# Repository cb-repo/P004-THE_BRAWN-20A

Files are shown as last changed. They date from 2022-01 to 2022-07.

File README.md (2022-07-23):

# THE BRAWN v1.0

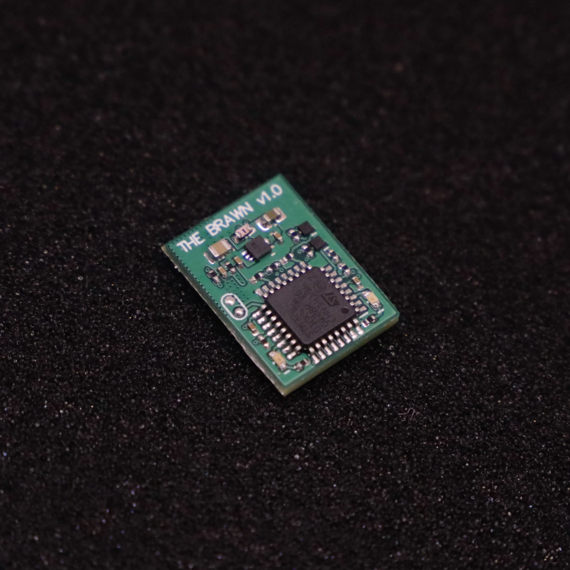
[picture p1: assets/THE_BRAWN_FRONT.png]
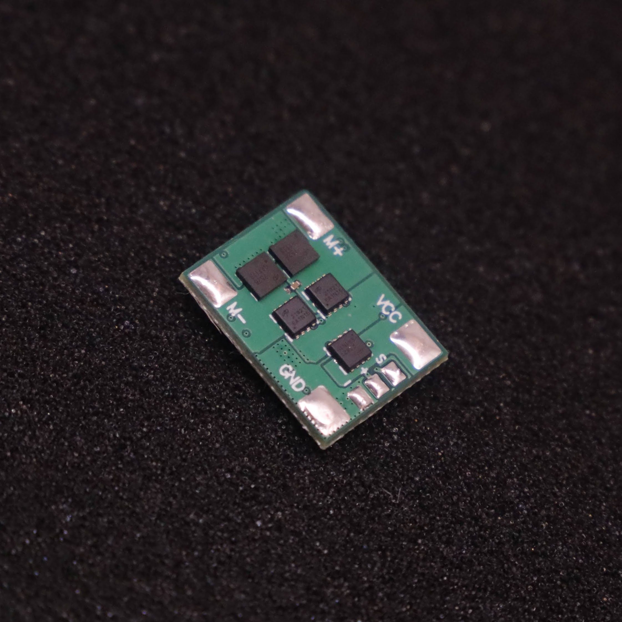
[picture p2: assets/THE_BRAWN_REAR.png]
 

THE BRAWN is a single DC-motor ESC: originally designed for insect-weight combat-robots, but is suitable for any appliction requiring a lightweight motor driver. 

Designed and built in [Christchurch, New Zealand ](https://www.google.co.nz/maps/place/Christchurch+New+Zealand) by Connor Benton, visit [cb-technology](https://www.cb-technology.co.nz/) for details.

## FEATURES
- Single Bi-Directional DC-motor output.
- Ultra-compact and lightweight.
- Under-voltage and reverse-polarity battery input protections.
- Run and status LED's.
- Instant power on and brown out recovery.
- Internal BEC for recievers.
- Includes a 100nF capacitor across the motor output to filter noise and voltage spikes.

## SPECIFICATIONS
- **Dimensions:** 20x15x4 mm
- **Weight:** 1.7g *excluding wires*
- **Input Voltage - Rated:** 1-3S lipo (3.3-12.6V)
- **Input Voltage - Absolute Max:** 18V
- **Output Current - Continuious:** 10A *(for more infomation see the Current Rating seciton)*
- **Output Current - Pulse:** 66A 
- **Motor Braking:** Enabled
- **BEC:** 3.3V, 200mA. Designed to power the radio reciever and other downstream ESC's but no motors or servos.
- **Signal Input:** Standard Servo PWM
     
## Fault Conditions
 - **Under-Voltage:** An under-voltage event occurs when the battery voltage falls below a pre-determined threshold.
    - At 3.6V (per cell) the device enters a warning state. This is only a warning and so functionality is not affected but the warning LED is illuminated for the operator.
    - At 3.4V (per cell) the device enters an under-voltage fault state. All motor functionality will be stopped until battery voltage is restored.
 - **Signal-Input:** A signal-input fault will occur if connection to the radio is lost for 50 ms. 
    - During a signal-input fault, a 'No Signal' fail-safe method is implemented and THE BRAWN will stop driving the motor output.
    - When a radio connection has been re-established the motor functionality is immediately resumed.

## LED Behaviour
There are two LEDs on THE BRAWN: 1x red Run LED and 1x green Status LED. The behaviour of each LED indicates what state the device is in.
 - **Normal Operation** Red: ON, Green: OFF
 - **Warning: Low Battery** Red: ON, Green: Flash
 - **Fault: Under-Voltage:** Red: Flash, Green: Flash
 - **Fault: Signal Input:** Red: OFF, Green: Flash

## Current Rating
The current rating of THE BRAWN is temperature-limited and so is very dependednt on the wires (gauge, length, and insulation) and avalible cooling. It is the responsibility of the user to choose the correct wires and test it appropriately before stressing the THE BRAWN in combat. 

As a guide, constant-current thermal testing has been conducted to illistrate the thermal characteristics. *Note: This test has been conducted at constant current, resulting in a higher temperature than the pulse currents in many drive applications.*

##### Reference testing parameters:
 - **Voltage:** 12V
 - **Motor Wire Length:** 100 mm
 - **Battery Wire Length:** 100 mm
 - **Wire Insulation:** PVC
 - **Ambient Temperature:** 23.5 °C
 - **PCB Heatshrink:** Yes
 - **ESC Cooling:** Open-Air passive cooling

##### Constant Current = 5A

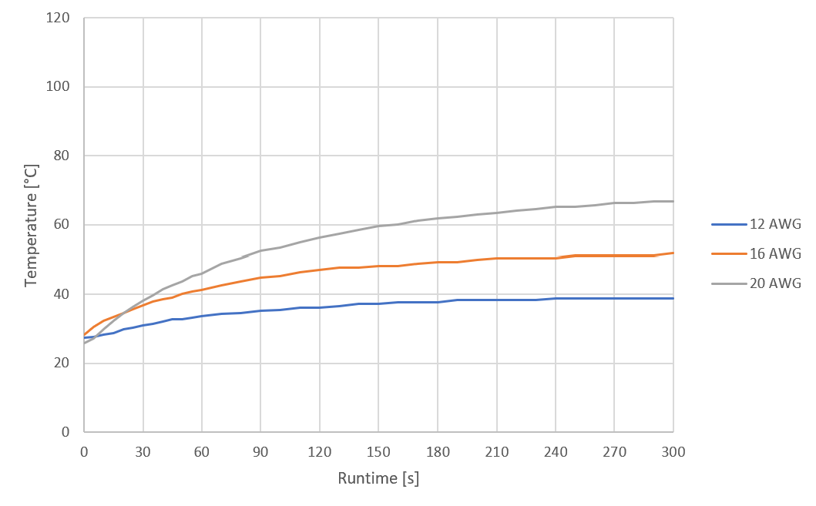
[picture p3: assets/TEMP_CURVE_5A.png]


##### Constant Current = 8A

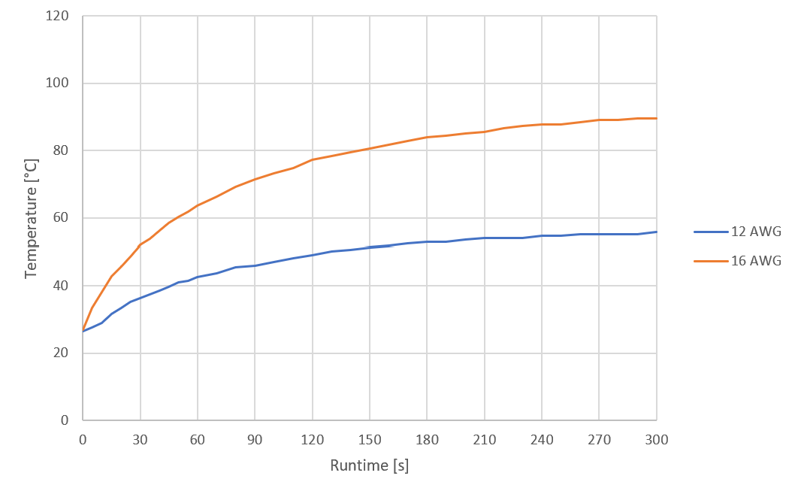
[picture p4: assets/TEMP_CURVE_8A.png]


##### Constant Current = 10A

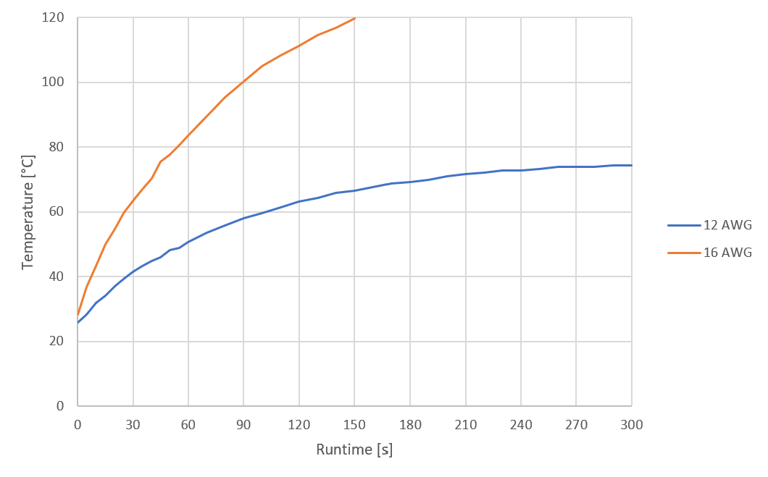
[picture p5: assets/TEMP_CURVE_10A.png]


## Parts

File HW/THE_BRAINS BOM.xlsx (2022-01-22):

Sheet: BOM Report
 |  |  | InFact Ltd.
 |  |  | 5 Amuri Park
 |  |  | 404 Barbadoes Street
 |  |  | Christchurch 8013
 |  |  | New Zealand
 |  | www.infact.co.nz
Bill of Materials |  |  | PXXX-50X - Description
Line | Manufacturer | Manufacturer Part Number | Description | Supplier 1 | Supplier Part Number 1 | Unit Price | Qty | Cost | Ordered | Received | Designator
1 | STMicroelectronics | STM32L051C6T6 | IC MCU 32BIT 32KB FLASH 48LQFP | Digi-Key | 497-15202-ND | $4.82 | 1 | $4.82 | Y | Y | U4
2 | STMicroelectronics | LDL212PUR | IC REG LINEAR POS ADJ 1.2A 6DFN | Digi-Key | 497-16566-1-ND | $0.58 | 1 | $0.58 | Y | Y | U2
3 | Texas Instruments | DRV8837CDSGR | IC HALF-BRIDGE DRVR PWM 8WSON | Digi-Key | 296-47205-1-ND | $1.21 | 2 | $2.42 | Y | Y | U6, U7
4 | Rohm Semiconductor | RQ3E120ATTB | MOSFET P-CH 30V 12A 8HSMT | Digi-Key | RQ3E120ATTBCT-ND | $0.90 | 1 | $0.90 | Y | Y
5 | Murata Electronics North America | BLM15HG102SN1D | FILTER CHIP 1000 OHM 250MA 0402 | Digi-Key | 490-3999-1-ND | $0.06 | 1 | $0.06 |  |  | L1
6 | Stackpole Electronics Inc | CSR0402FKR100 | RES 0.1 OHM 1% 1/8W 0402 | Digi-Key | CSR0402FKR100CT-ND | $0.18 | 1 | $0.18 | Y |  | R2
7 | Samsung Electro-Mechanics | CL21A106KAYNNNG | CAP CER 10UF 25V X5R 0805 | Digi-Key | 1276-6454-1-ND | $0.11 | 1 | $0.11 | Y |  | C7
8 | Bourns Inc. | MF-FSMF020X-2 | PTC RESET FUSE 9V 200MA 0603 | Digi-Key | MF-FSMF020X-2CT-ND | $0.50 | 1 | $0.50 | Y |  | R4
9 | Taiyo Yuden | UMK105CBJ105MV-F | CAP CER 1UF 50V X5R 0402 | Digi-Key | 587-6278-1-ND | $0.16 | 2 | $0.33 | Y | Y | C8, C4
10 | KYOCERA AVX | 0402YD475MAT2A | CAP CER 4.7UF 16V X5R 0402 | Digi-Key | 478-10788-1-ND | $0.18 | 1 | $0.18 | Y | Y | C12
11 | Taiyo Yuden | UMK105B7104KV-FR | CAP CER 0.1UF 50V X7R 0402 | Digi-Key | 587-3498-1-ND | $0.05 | 12 | $0.60 | Y | Y | C1, C2, C6, C9, C10, C11, C13, C15, C18, C19, C20, C21
12 | Lumex Opto/Components Inc | SML-LX0603GW-TR | LED 565NM GRN DIFF 0603 SMD | Digi-Key | 67-1549-1-ND | $0.23 | 1 | $0.23 | Y | Y | DS2
13 | Lumex Opto/Components Inc | SML-LX0603IW-TR | LED 635NM RED DIFF 0603 SMD | Digi-Key | 67-1548-1-ND | $0.23 | 1 | $0.23 | Y | Y | DS1
14 | Vishay Dale | CRCW04021K80FKED | RES 1k8 0.0625W 1% 0402 SMD | Digi-Key | 541-1.80KLCT-ND | $0.01 | 1 | $0.01 | Y | Y | R8
15 | Yageo | RC0402FR-0710KL | RES 10K OHM 1/16W 1% 0402 SMD | Digi-Key | 311-10.0KLRCT-ND | $0.00385 | 7 | $0.03 | Y | Y | R7, R9, R10, R11, R12, R13, R14
16 | Yageo | RC0402FR-07120RL | RES 120 OHM 1/16W 0402 SMD | Digi-Key | 311-120LRCT-ND | $0.00385 | 2 | $0.01 | Y | Y | R5, R15
17 | Yageo | RC0402FR-07150KL | RES SMD 150K OHM 1% 1/16W 0402 | Digi-Key | 311-150KLRCT-ND | $0.01 | 1 | $0.01 | Y | Y | R3
18 | Yageo | RC0402FR-07270KL | RES SMD 270K OHM 1% 1/16W 0402 | Digi-Key | 311-270KLRCT-ND | $0.01 | 1 | $0.01 | Y | Y | R1
19 | JLC PCB |  | PCB |  |  | $5.68 | 1 | $5.68 | Y
20 | Chip Quik Inc. | SMD291AX50T3 | SLDR PASTE NO-CLN SN63/PB37 50G | Digi-Key | SMD291AX50T3-ND | $0.21 | 1 | $0.21 | Y | Y
 |  |  |  |  |  |  | 31 | $17.08
Approved |  |  | Notes
 | Total Order Cost
 | Total Order QTY | 60
 | Unit Cost | $17.08
 | Unit Sell Price | 30
 | Unit Profit | 12.91864
 | Total Profit | 775.1184

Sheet: Sheet1
MCU + FETs | 430.39 | 50 | 8.6078
LDO |  |  | 0.684
Poly-fuse | - | - | 0.4951
22UF Cap | - | - | 0.2248
LED x2 |  |  | 0.4634
Passives |  |  | 0.1282
Solder Paste | - | - | 0.1
PCB | 284.16 | 50 | 5.6832
Assy Labour | 250 | 50 | 5
 |  |  | 21.3865 | Unit Cost
 |  |  | 30 | Unit Sale Price
 |  |  | 8.6135 | Unit Profit
 |  |  | 430.675 | Total Profit

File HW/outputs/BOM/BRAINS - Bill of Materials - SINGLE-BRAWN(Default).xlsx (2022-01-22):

 |  |  | InFact Ltd. | +64 3 3777316
 |  |  | 5 Amuri Park | <Parameter Project_Fax not found>
 |  |  | 404 Barbadoes Street
 |  |  | Christchurch 8013
 |  |  | New Zealand
 |  | www.infact.co.nz
Bill of Materials |  |  | PXXX-50X - Description
Source Data From: |  |  | C:\dev\GitHub\THE_BRAWN\HW\BRAWN.PrjPCB
Project: |  |  | BRAWN.PrjPCB
Revision: |  |  | 0A
Variant: |  |  | Default
Creation Date: |  | 9/12/2021 | 2:01 AM
Print Date: |  | 2021-12-09 | 2:01:45
Line | Manufacturer | Manufacturer Part Number | Description | Fitted | Supplier 1 | Supplier Part Number 1 | Supplier Unit Price 1 | Quantity | Cost | Designator
1 | Taiyo Yuden | UMK105B7104KV-FR | CAP CER 100nF 50V X7R 0402 | Fitted | Digi-Key | 587-3498-1-ND | $0.04 | 1 | $0.04 | C2
2 | Taiyo Yuden | UMK105B7104KV-FR | CAP CER 100nF 50V X7R 0402 | Fitted | Digi-Key | 587-3498-1-ND | $0.04 | 1 | $0.04 | C4
3 | Taiyo Yuden | UMK105B7104KV-FR | CAP CER 100nF 50V X7R 0402 | Fitted | Digi-Key | 587-3498-1-ND | $0.04 | 1 | $0.04 | C8
4 | Taiyo Yuden | UMK105B7104KV-FR | CAP CER 100nF 50V X7R 0402 | Fitted | Digi-Key | 587-3498-1-ND | $0.04 | 1 | $0.04 | C9
5 | Taiyo Yuden | UMK105B7104KV-FR | CAP CER 100nF 50V X7R 0402 | Fitted | Digi-Key | 587-3498-1-ND | $0.04 | 1 | $0.04 | C10
6 | Taiyo Yuden | UMK105B7104KV-FR | CAP CER 100nF 50V X7R 0402 | Fitted | Digi-Key | 587-3498-1-ND | $0.04 | 1 | $0.04 | C12
7 | Samsung Electro-Mechanics | CL21A226KOQNNNE | CAP CER 22UF 16V X5R 0805 | Fitted | Digi-Key | 1276-6526-1-ND | $0.14 | 1 | $0.14 | C3
8 | Samsung Electro-Mechanics | CL21A226KOQNNNE | CAP CER 22UF 16V X5R 0805 | Fitted | Digi-Key | 1276-6526-1-ND | $0.14 | 1 | $0.14 | C7
9 | STMicroelectronics | LDL212PV33R | 1.2A 3V3 LDO LINEAR REGULATOR | Fitted | Digi-Key | 497-19548-1-ND | $0.36 | 1 | $0.36 | U1
10 | STMicroelectronics | STM32L010K4T6 | ARM® Cortex®-M0+ series Microcontroller IC 32-Bit 32MHz 16KB (16K x 8) FLASH 32-LQFP (7x7) | Fitted | Digi-Key | 497-STM32L010K4T6-ND | $1.69 | 1 | $1.69 | U3
11 | Lumex Opto/Components Inc | SML-LX0603GW-TR | LED 565NM GRN DIFF 0603 SMD | Fitted | Digi-Key | 67-1549-1-ND | $0.13 | 1 | $0.13 | DS2
12 | Lumex Opto/Components Inc | SML-LX0603IW-TR | LED 635NM RED DIFF 0603 SMD | Fitted | Digi-Key | 67-1548-1-ND | $0.13 | 1 | $0.13 | DS1
13 |  |  |  | Fitted |  |  |  | 1 | $0.00 | J1
14 |  |  |  | Fitted |  |  |  | 1 | $0.00 | J2
15 |  |  |  | Fitted |  |  |  | 1 | $0.00 | J3
16 |  |  |  | Fitted |  |  |  | 1 | $0.00 | J4
17 |  |  |  | Fitted |  |  |  | 1 | $0.00 | J5
18 |  |  |  | Fitted |  |  |  | 1 | $0.00 | J7
19 |  |  |  | Fitted |  |  |  | 1 | $0.00 | J8
20 |  |  |  | Fitted |  |  |  | 1 | $0.00 | J9
21 |  |  |  | Fitted |  |  |  | 1 | $0.00 | J10
22 | Yageo | RC0402JR-070RL | RES 0R OHM 1/16W 5% 0402 SMD | Fitted | Digi-Key | 311-0.0JRCT-ND | $0.00313 | 1 | $0.00313 | R1
23 | Vishay Dale | CRCW04021K80FKED | RES 1k8 0.0625W 1% 0402 SMD | Fitted | Digi-Key | 541-1.80KLCT-ND | $0.01 | 1 | $0.01 | R13
24 | Yageo | RC0402FR-0710KL | RES 10K OHM 1/16W 1% 0402 SMD | Fitted | Digi-Key | 311-10.0KLRCT-ND | $0.00441 | 1 | $0.00441 | R4
25 | Yageo | RC0402FR-0710KL | RES 10K OHM 1/16W 1% 0402 SMD | Fitted | Digi-Key | 311-10.0KLRCT-ND | $0.00441 | 1 | $0.00441 | R6
26 | Yageo | RC0402FR-0710KL | RES 10K OHM 1/16W 1% 0402 SMD | Fitted | Digi-Key | 311-10.0KLRCT-ND | $0.00441 | 1 | $0.00441 | R7
27 | Yageo | RC0402FR-0710KL | RES 10K OHM 1/16W 1% 0402 SMD | Fitted | Digi-Key | 311-10.0KLRCT-ND | $0.00441 | 1 | $0.00441 | R8
28 | Yageo | RC0402FR-0710KL | RES 10K OHM 1/16W 1% 0402 SMD | Fitted | Digi-Key | 311-10.0KLRCT-ND | $0.00441 | 1 | $0.00441 | R9
29 | Yageo | RC0402FR-0710KL | RES 10K OHM 1/16W 1% 0402 SMD | Fitted | Digi-Key | 311-10.0KLRCT-ND | $0.00441 | 1 | $0.00441 | R10
30 | Yageo | RC0402FR-0710KL | RES 10K OHM 1/16W 1% 0402 SMD | Fitted | Digi-Key | 311-10.0KLRCT-ND | $0.00441 | 1 | $0.00441 | R11
31 | Yageo | RC0402FR-0710KL | RES 10K OHM 1/16W 1% 0402 SMD | Fitted | Digi-Key | 311-10.0KLRCT-ND | $0.00441 | 1 | $0.00441 | R12
32 | Yageo | RC0402FR-07120RL | RES 120 OHM 1/16W 0402 SMD | Fitted | Digi-Key | 311-120LRCT-ND | $0.00441 | 1 | $0.00441 | R14
33 | Yageo | RC0402FR-07120RL | RES 120 OHM 1/16W 0402 SMD | Fitted | Digi-Key | 311-120LRCT-ND | $0.00441 | 1 | $0.00441 | R15
34 | Yageo | RC0603JR-070RL | RES 0.0 OHM 1/10W 0603 SMD | Fitted | Digi-Key | 311-0.0GRCT-ND | $0.00462 | 1 | $0.00462 | R2
35 | Alpha & Omega Semiconductor Inc. | AONR21321 | P-Channel 30 V 24A (Tc) 4.1W (Ta), 24W (Tc) Surface Mount 8-DFN-EP (3x3) | Fitted | Digi-Key | 785-1797-1-ND | $0.28 | 1 | $0.28 | Q1
36 | Alpha & Omega Semiconductor Inc. | AONR21321 | P-Channel 30 V 24A (Tc) 4.1W (Ta), 24W (Tc) Surface Mount 8-DFN-EP (3x3) | Fitted | Digi-Key | 785-1797-1-ND | $0.28 | 1 | $0.28 | Q3
37 | Alpha & Omega Semiconductor Inc. | AONR21321 | P-Channel 30 V 24A (Tc) 4.1W (Ta), 24W (Tc) Surface Mount 8-DFN-EP (3x3) | Fitted | Digi-Key | 785-1797-1-ND | $0.28 | 1 | $0.28 | Q4
38 | Alpha & Omega Semiconductor Inc. | AON7528 | MOSFET N-CH 30V 45A/50A 8DFN | Fitted | Digi-Key | 785-1506-1-ND | $0.64 | 1 | $0.64 | Q6
39 | Alpha & Omega Semiconductor Inc. | AON7528 | MOSFET N-CH 30V 45A/50A 8DFN | Fitted | Digi-Key | 785-1506-1-ND | $0.64 | 1 | $0.64 | Q7
40 | Diodes Incorporated | DMN2450UFD-7 | MOSFET N-CH 20V 900MA 3DFN | Fitted | Digi-Key | DMN2450UFD-7DICT-ND | $0.11 | 1 | $0.11 | Q2
41 | Diodes Incorporated | DMN2450UFD-7 | MOSFET N-CH 20V 900MA 3DFN | Fitted | Digi-Key | DMN2450UFD-7DICT-ND | $0.11 | 1 | $0.11 | Q5
 |  |  |  |  |  |  |  | 41 | $5.22
Approved |  |  | Notes

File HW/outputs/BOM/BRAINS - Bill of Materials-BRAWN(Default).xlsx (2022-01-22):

 |  |  | InFact Ltd. | +64 3 3777316
 |  |  | 5 Amuri Park | <Parameter Project_Fax not found>
 |  |  | 404 Barbadoes Street
 |  |  | Christchurch 8013
 |  |  | New Zealand
 |  | www.infact.co.nz
Bill of Materials |  |  | PXXX-50X - Description
Source Data From: |  |  | C:\dev\GitHub\THE_BRAWN\HW\BRAWN.PrjPCB
Project: |  |  | BRAWN.PrjPCB
Revision: |  |  | 0A
Variant: |  |  | Default
Creation Date: |  | 9/12/2021 | 2:01 AM
Print Date: |  | 2021-12-09 | 2:01:49
Line | Manufacturer | Manufacturer Part Number | Description | Fitted | Supplier 1 | Supplier Part Number 1 | Supplier Unit Price 1 | Quantity | Cost | Designator
1 | Taiyo Yuden | UMK105B7104KV-FR | CAP CER 100nF 50V X7R 0402 | Fitted | Digi-Key | 587-3498-1-ND | $0.03 | 6 | $0.19 | C2, C4, C8, C9, C10, C12
2 | Samsung Electro-Mechanics | CL21A226KOQNNNE | CAP CER 22UF 16V X5R 0805 | Fitted | Digi-Key | 1276-6526-1-ND | $0.14 | 2 | $0.28 | C3, C7
3 | STMicroelectronics | LDL212PV33R | 1.2A 3V3 LDO LINEAR REGULATOR | Fitted | Digi-Key | 497-19548-1-ND | $0.36 | 1 | $0.36 | U1
4 | STMicroelectronics | STM32L010K4T6 | ARM® Cortex®-M0+ series Microcontroller IC 32-Bit 32MHz 16KB (16K x 8) FLASH 32-LQFP (7x7) | Fitted | Digi-Key | 497-STM32L010K4T6-ND | $1.69 | 1 | $1.69 | U3
5 | Lumex Opto/Components Inc | SML-LX0603GW-TR | LED 565NM GRN DIFF 0603 SMD | Fitted | Digi-Key | 67-1549-1-ND | $0.13 | 1 | $0.13 | DS2
6 | Lumex Opto/Components Inc | SML-LX0603IW-TR | LED 635NM RED DIFF 0603 SMD | Fitted | Digi-Key | 67-1548-1-ND | $0.13 | 1 | $0.13 | DS1
7 |  |  |  | Fitted |  |  |  | 9 | $0.00 | J1, J2, J3, J4, J5, J7, J8, J9, J10
8 | Yageo | RC0402JR-070RL | RES 0R OHM 1/16W 5% 0402 SMD | Fitted | Digi-Key | 311-0.0JRCT-ND | $0.00313 | 1 | $0.00313 | R1
9 | Vishay Dale | CRCW04021K80FKED | RES 1k8 0.0625W 1% 0402 SMD | Fitted | Digi-Key | 541-1.80KLCT-ND | $0.01 | 1 | $0.01 | R13
10 | Yageo | RC0402FR-0710KL | RES 10K OHM 1/16W 1% 0402 SMD | Fitted | Digi-Key | 311-10.0KLRCT-ND | $0.00316 | 8 | $0.03 | R4, R6, R7, R8, R9, R10, R11, R12
11 | Yageo | RC0402FR-07120RL | RES 120 OHM 1/16W 0402 SMD | Fitted | Digi-Key | 311-120LRCT-ND | $0.00441 | 2 | $0.01 | R14, R15
12 | Yageo | RC0603JR-070RL | RES 0.0 OHM 1/10W 0603 SMD | Fitted | Digi-Key | 311-0.0GRCT-ND | $0.00462 | 1 | $0.00462 | R2
13 | Alpha & Omega Semiconductor Inc. | AONR21321 | P-Channel 30 V 24A (Tc) 4.1W (Ta), 24W (Tc) Surface Mount 8-DFN-EP (3x3) | Fitted | Digi-Key | 785-1797-1-ND | $0.25 | 3 | $0.75 | Q1, Q3, Q4
14 | Alpha & Omega Semiconductor Inc. | AON7528 | MOSFET N-CH 30V 45A/50A 8DFN | Fitted | Digi-Key | 785-1506-1-ND | $0.64 | 2 | $1.29 | Q6, Q7
15 | Diodes Incorporated | DMN2450UFD-7 | MOSFET N-CH 20V 900MA 3DFN | Fitted | Digi-Key | DMN2450UFD-7DICT-ND | $0.11 | 2 | $0.23 | Q2, Q5
 |  |  |  |  |  |  |  | 41 | $5.10
Approved |  |  | Notes

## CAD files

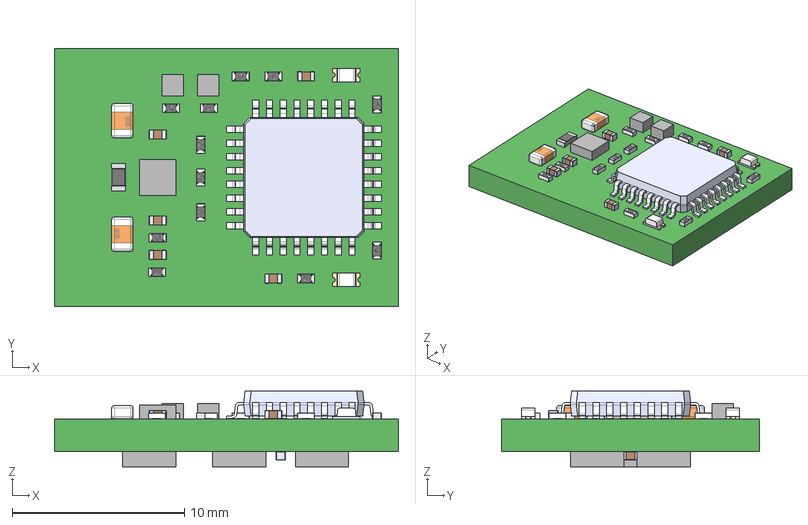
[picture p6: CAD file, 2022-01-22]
HW/outputs/ExportSTEP/BRAWN(Default).step
20.0 x 15.0 x 4.41 mm
TSQFP50P700X700X160-32N
Extruded x 8
User_Library-RESC1005X04N x 12
User_Library-res0603-1
LED_0603 x 2
EVK105RH010BW-F--3DModel-STEP-46669 x 6
User_Library-0805_SMD_Capacitor x 2

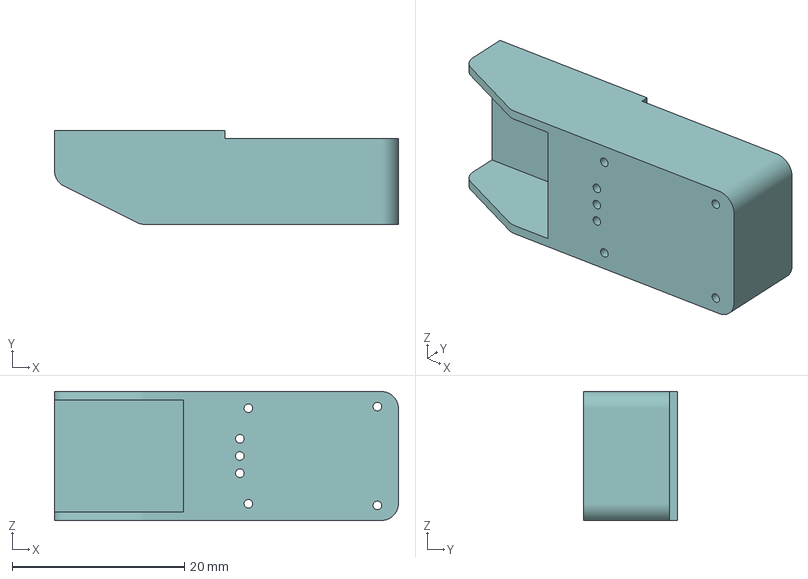
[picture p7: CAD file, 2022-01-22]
MECH/Programmer ClipBottom.3MF
40.0 x 10.9 x 15.0 mm

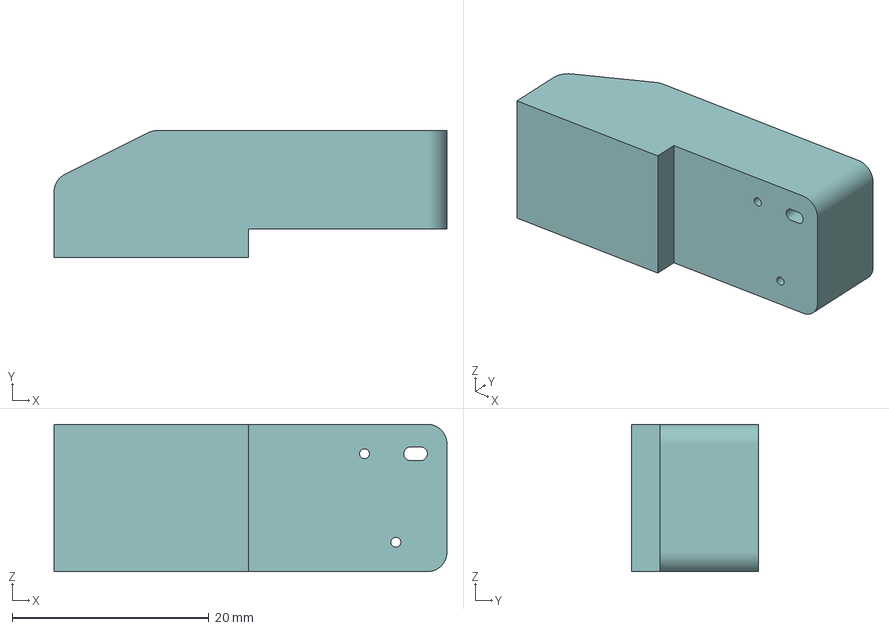
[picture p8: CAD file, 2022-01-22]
MECH/Programmer ClipTop.3MF
40.0 x 12.9 x 15.0 mm

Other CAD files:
MECH/Programmer Clip.SLDPRT

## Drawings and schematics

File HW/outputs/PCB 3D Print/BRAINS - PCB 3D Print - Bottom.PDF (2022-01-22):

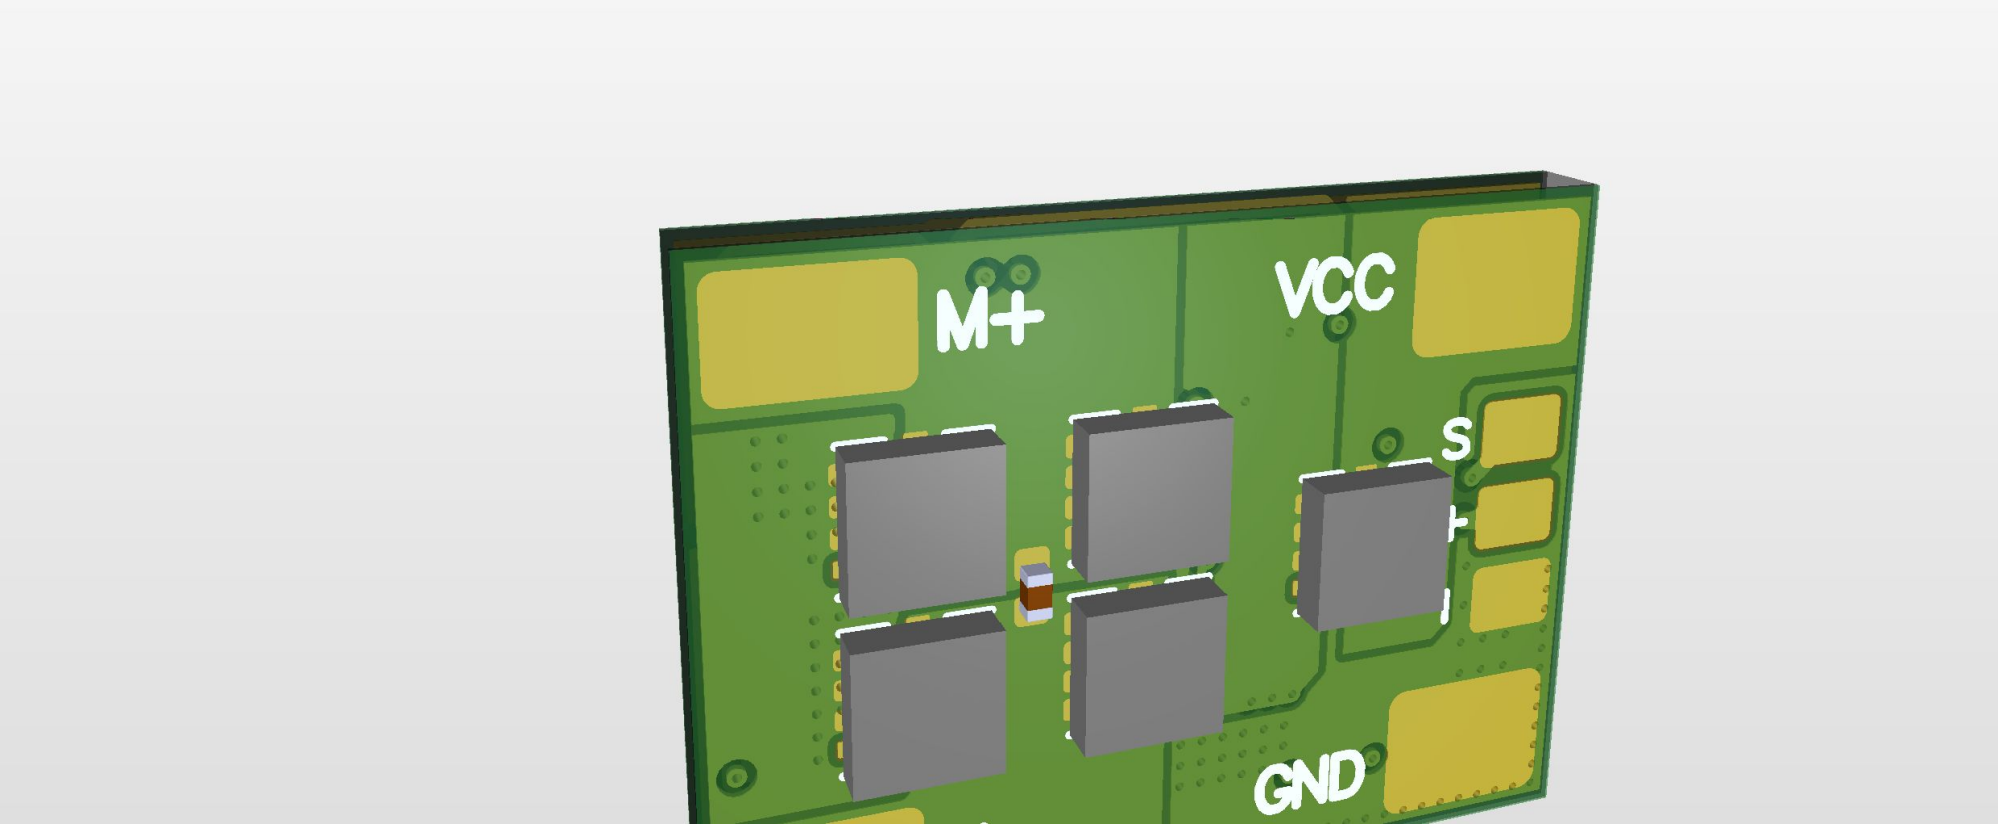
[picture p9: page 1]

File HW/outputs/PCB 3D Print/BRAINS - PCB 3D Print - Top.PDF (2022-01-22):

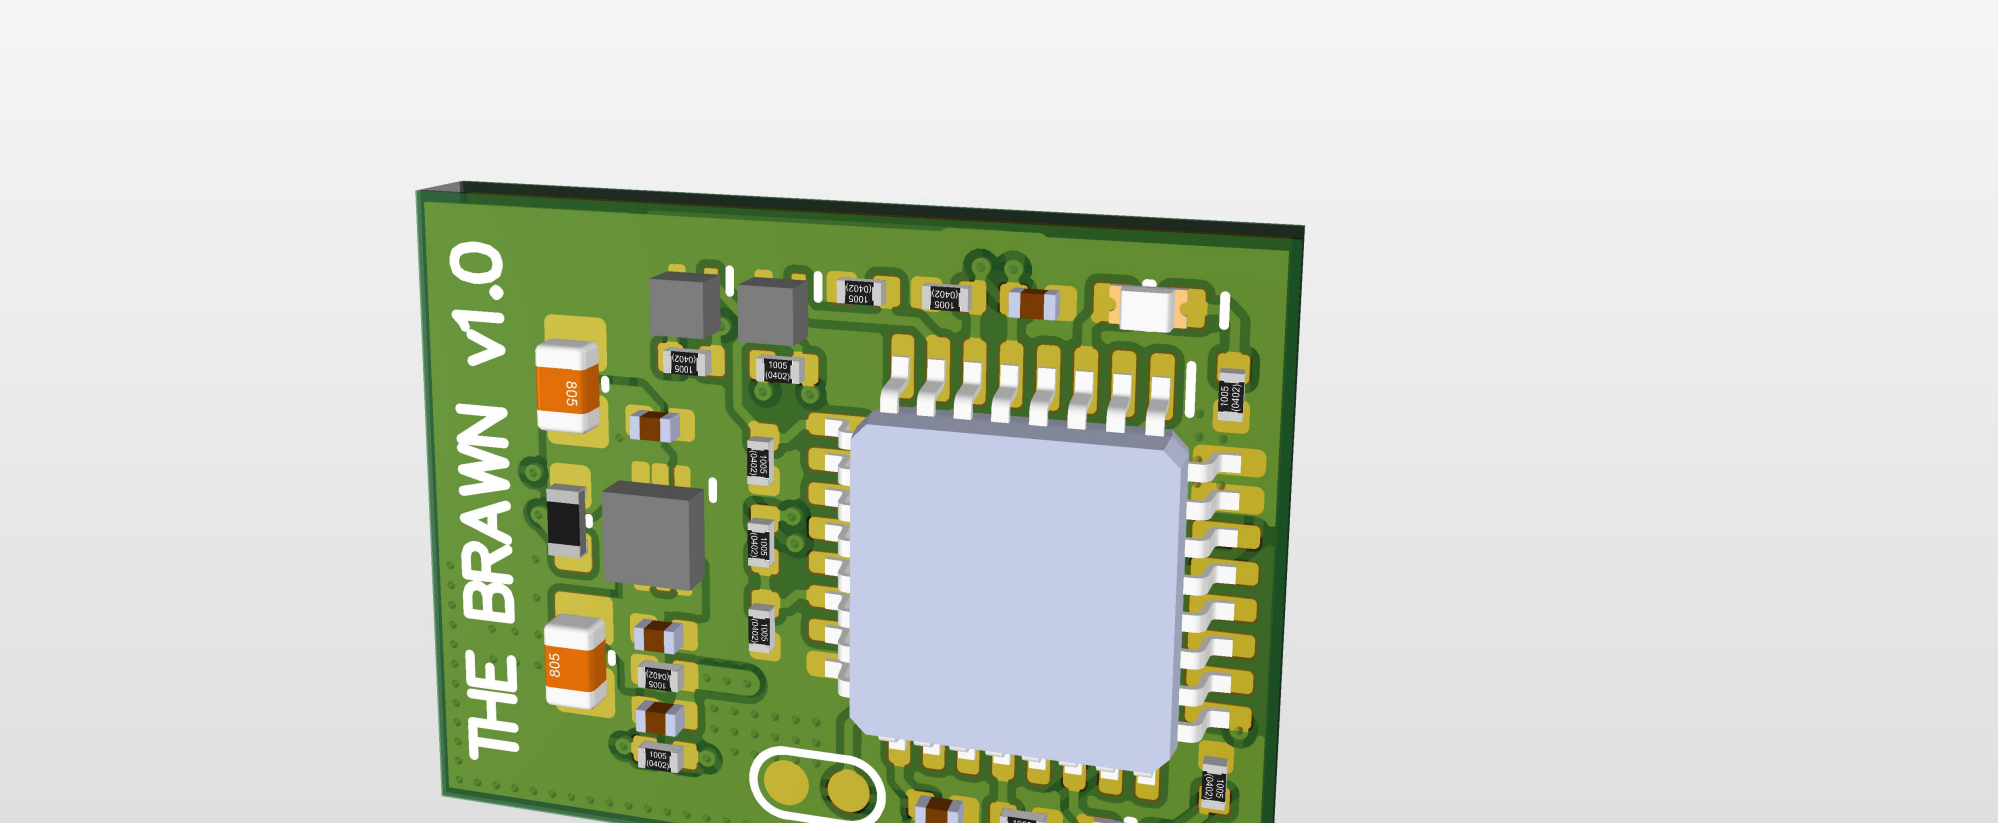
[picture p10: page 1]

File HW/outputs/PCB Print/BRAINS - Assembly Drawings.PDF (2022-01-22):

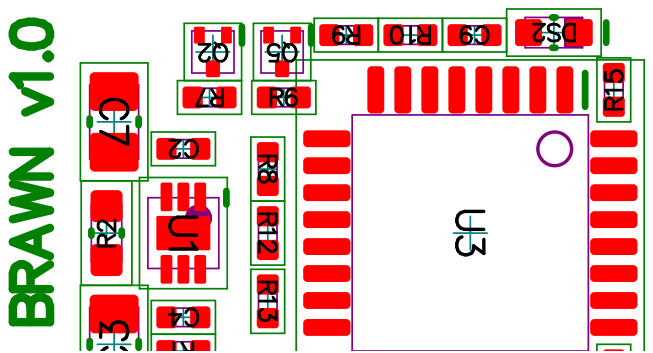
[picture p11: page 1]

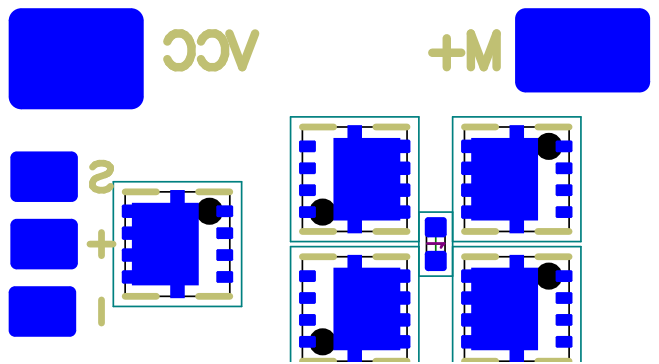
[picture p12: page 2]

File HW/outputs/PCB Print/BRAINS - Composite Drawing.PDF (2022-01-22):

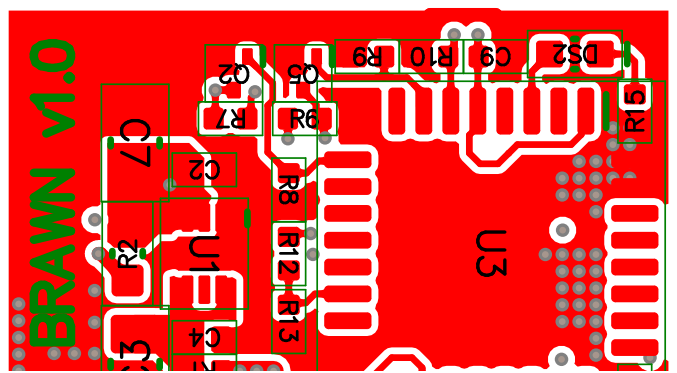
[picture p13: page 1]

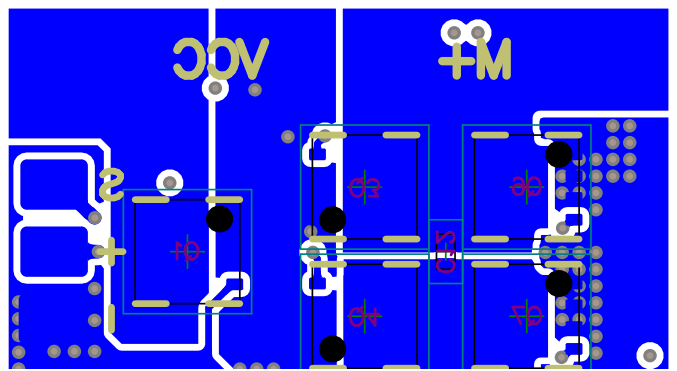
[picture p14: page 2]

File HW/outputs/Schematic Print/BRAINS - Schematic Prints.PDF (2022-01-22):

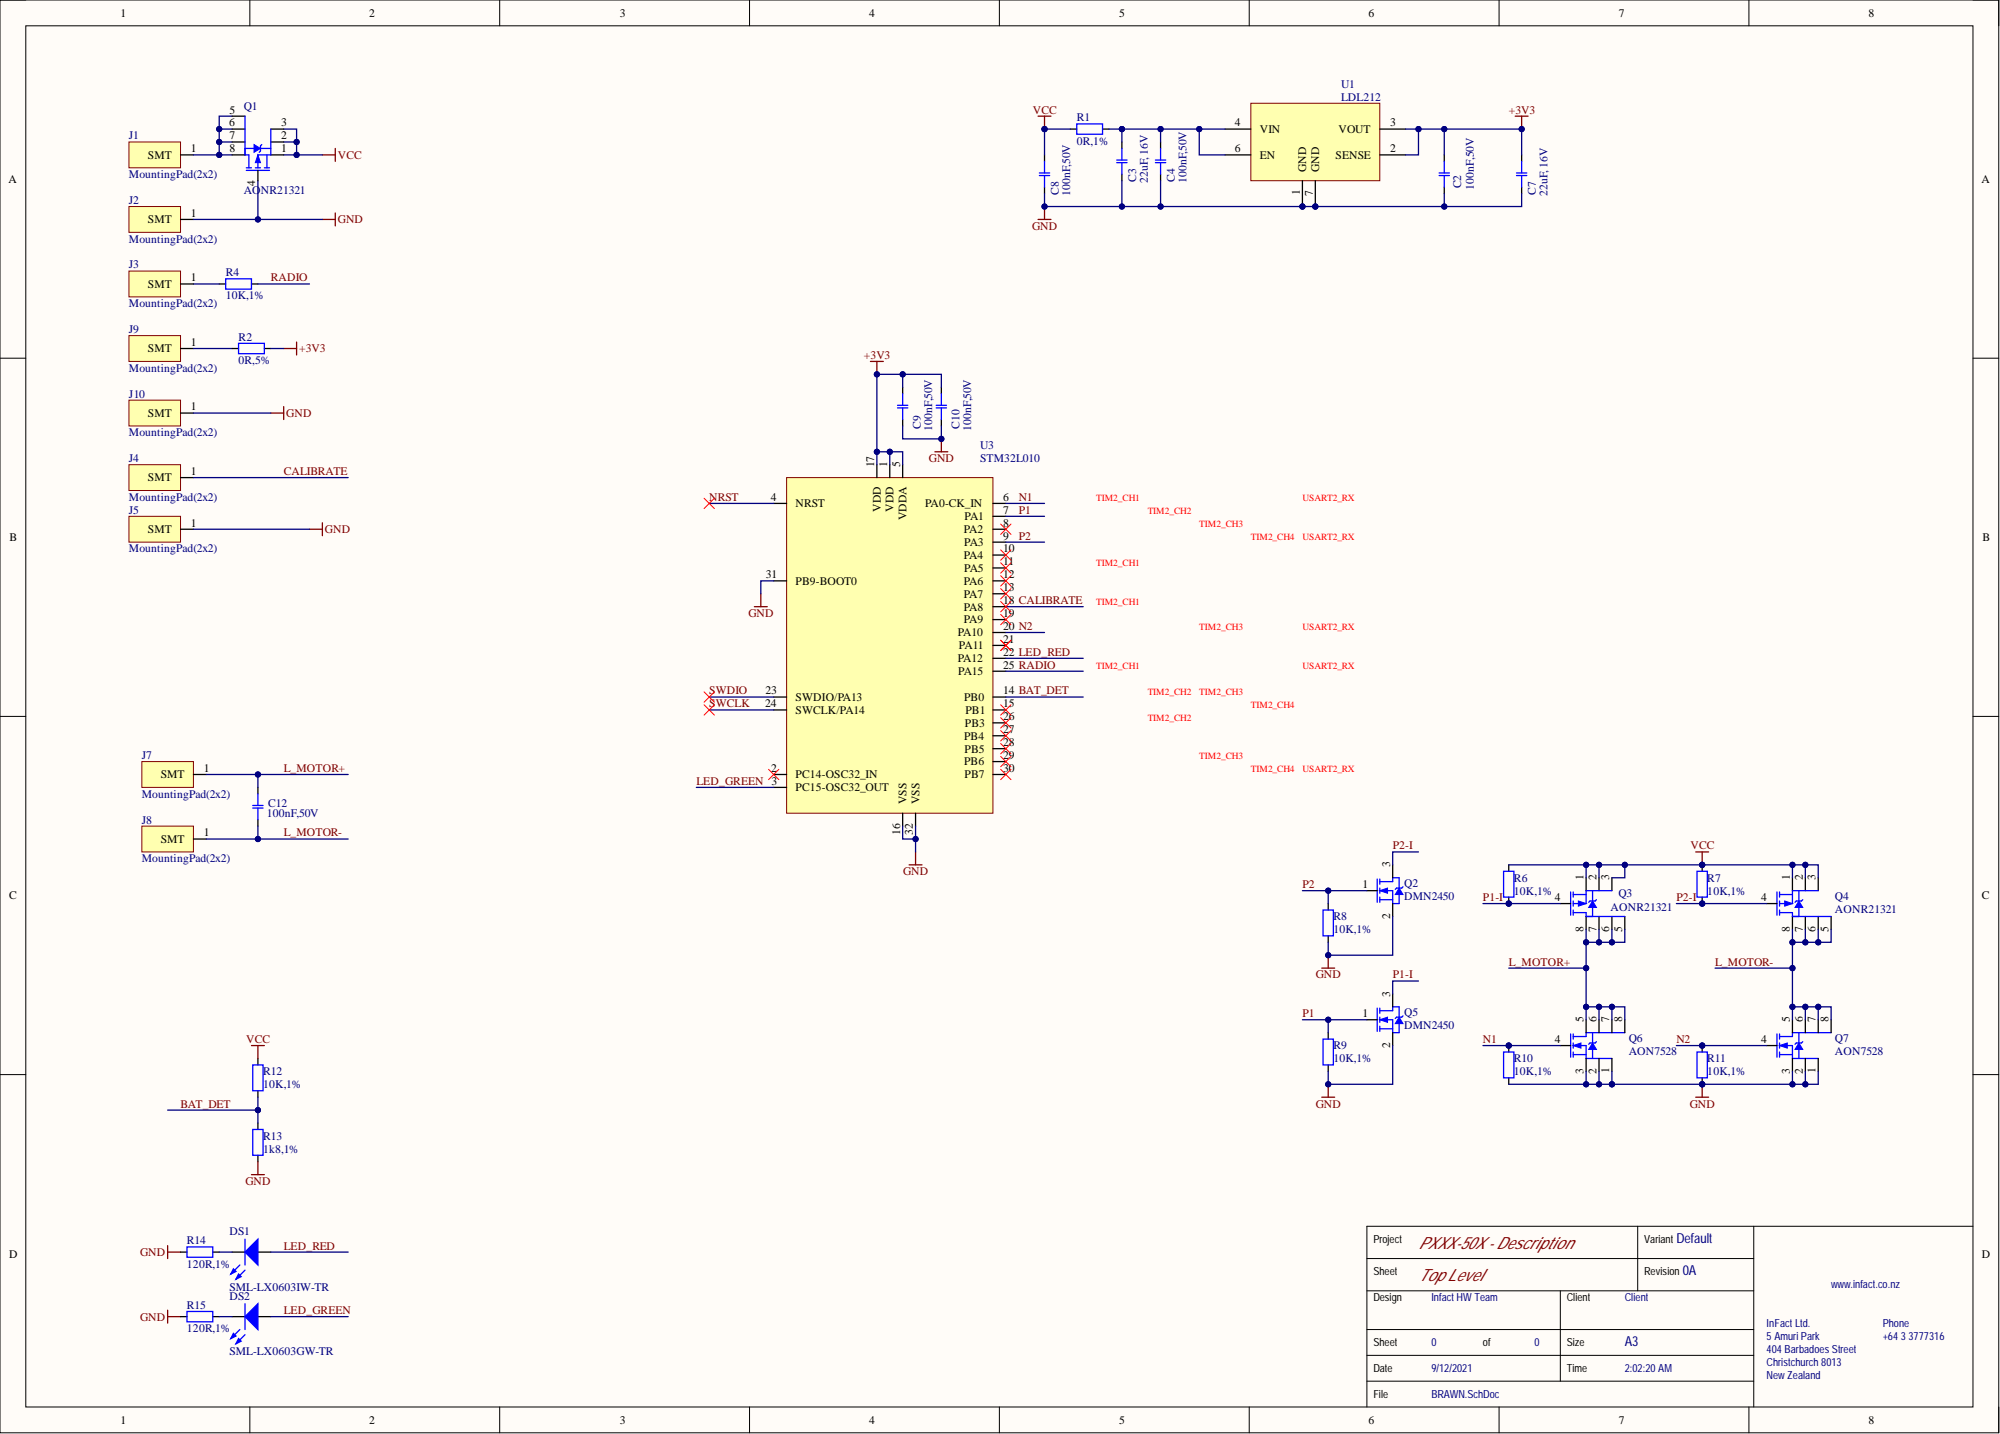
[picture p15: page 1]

Top | Revi sion 0A

www.infact.co.nz

Infact HW Team | Cl ient

InFact Ltd.
5 Amuri Park
404 Barbadoes Street Christchurch 8013 New Zealand

Sheet 0 of 0 | A3 Si ze

Date 9/12/2021 | Time 2:02:20 AM

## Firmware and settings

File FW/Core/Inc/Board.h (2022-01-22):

/* ~~~~~~~~~~~~~~~~~~~~~~~~~~~~~~~~~~~~~~~~~~~~~~~~~~ */
#ifndef BOARD_H
#define BOARD_H
/* ~~~~~~~~~~~~~~~~~~~~~~~~~~~~~~~~~~~~~~~~~~~~~~~~~~ */

#include "STM32X.h"

#define STM32L0

// ADC CONFIG
#define ADC_VREF	      	3300

#define CLK_PLL_DIV 		2

// TIM CONFIG
#define TIM_USE_IRQS
// 		Motor O/P
#define TIM2_ENABLE
#define TIM_MOTOR 			TIM_2
#define TIM_MOTOR_AF2		GPIO_AF2_TIM2
#define TIM_MOTOR_AF5		GPIO_AF5_TIM2
#define TIM_MOTOR_CH		0
#define TIM_MOTOR_RELOAD	500
#define TIM_MOTOR_FREQ		(((TIM_MOTOR_RELOAD + 1) * 1000) / MOTOR_PERIOD_MS) // (MOTOR_FREQ*(TIM_MOTOR_RELOAD+1))
// 		Radio I/P
#define TIM21_ENABLE
#define TIM_RADIO 			TIM_21
#define TIM_RADIO_RELOAD 	0xffff
#define TIM_RADIO_FREQ		1000000


// UART CONFIG
// 		USART1_Tx - Pin30 (PA9)
//		USART1_Rx - Pin31	(PA10)
#define UART2_GPIO			GPIOB
#define UART2_PINS			(GPIO_PIN_6 | GPIO_PIN_7)
#define UART2_AF		    GPIO_AF0_USART2
#define DEBUG_UART			UART_2
#define DEBUG_BAUD			115200
#define DEBUG_MODE			UART_Mode_Default
#define UART_BFR_SIZE     	16


// IRQ CONFIG
#define GPIO_USE_IRQS
#define GPIO_IRQ8_ENABLE
#define GPIO_IRQ15_ENABLE
// 		Calibrate I/P - Pin18 (PA8)
#define CALIBRATE_GPIO		GPIOA
#define	CALIBRATE_PIN		GPIO_PIN_8
// 		Radio I/P - Pin25 (PA15) USART2_Rx
#define RADIO_GPIO			GPIOA
#define RADIO_PIN			GPIO_PIN_15


// DC-MOTOR H-BRIDGE CONFIG
/*
 * VSS --------------
 *  	|			|
 *     	P1			P2
 *     	|			|
 *     	|-- MOTOR --|
 *     	|			|
 *     	N1			N2
 *     	|	`		|
 * VCC --------------
 *
 * Note: P1 and P2 are P-FET, controlled through 2x Additional N-FET on the gate
 */
//		N1-FET O/P - Pin6 (PA0) TIM2_CH1
#define FET_N1_GPIO			GPIOA
#define FET_N1_PIN			GPIO_PIN_0
//		N2-FET O/P - Pin20 (PA10) TIM2 CH3
#define FET_N2_GPIO			GPIOA
#define FET_N2_PIN			GPIO_PIN_10
//		P1-FET O/P - Pin7 (PA1) TIM2_CH2
#define FET_P1_GPIO			GPIOA
#define FET_P1_PIN			GPIO_PIN_1
//		P2-FET O/P - Pin9 (PA3) TIM2 CH4
#define FET_P2_GPIO			GPIOA
#define FET_P2_PIN			GPIO_PIN_3

// IO CONFIG
// 		Battery Detect - Pin14 (PB0)
#define BATTERY_GPIO		GPIOB
#define	BATTERY_PIN			GPIO_PIN_0
#define BATTERY_CHANNEL		ADC_CHANNEL_8
#define BATTERY_DET_RLOW	1800
#define BATTERY_DET_RHIGH	10000
// 		Green LED - Pin3 (PC15)
#define LED_GRN_GPIO		GPIOC
#define LED_GRN_PIN			GPIO_PIN_15
// 		Red LED - Pin22 (PA12)
#define LED_RED_GPIO		GPIOA
#define LED_RED_PIN			GPIO_PIN_12


#endif /* BOARD_H */
/* ~~~~~~~~~~~~~~~~~~~~~~~~~~~~~~~~~~~~~~~~~~~~~~~~~~ */

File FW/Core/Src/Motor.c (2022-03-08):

/* ~~~~~~~~~~~~~~~~~~~~~~~~~~~~~~~~~~~~~~~~~~~~~~~~~~ */

#include "Motor.h"
#include "GPIO.h"
#include "TIM.h"
#include "Core.h"
#include "Radio.h"
#include "System.h"

/*
 * PRIVATE DEFINITIONS
 */

#define MOTOR_BRAKING		true

/*
 * PRIVATE TYPES
 */


/*
 * PRIVATE PROTOTYPES
 */

void MOTOR_TurnOFF(void);
void MOTOR_UpdatePWM(int32_t);
void MOTOR_DirectionChanged(int32_t, bool);

void MOTOR_N1TimerPulseISR (void);
void MOTOR_N1TimerReloadISR (void);
void MOTOR_N2TimerPulseISR (void);
void MOTOR_N2TimerReloadISR (void);
void MOTOR_TimerBlankIRQ (void);

/*
 * PRIVATE VARIABLES
 */


/*
 * PUBLIC FUNCTIONS
 */

void MOTOR_Init (void)
{
	GPIO_EnableOutput(FET_P1_GPIO, FET_P1_PIN, GPIO_PIN_RESET);
	GPIO_EnableOutput(FET_P2_GPIO, FET_P2_PIN, GPIO_PIN_RESET);
	GPIO_EnableOutput(FET_N1_GPIO, FET_N1_PIN, GPIO_PIN_RESET);
	GPIO_EnableOutput(FET_N2_GPIO, FET_N2_PIN, GPIO_PIN_RESET);
}

/*
 * UPDATE THE MOTOR SPEED
 */
void MOTOR_Update (void)
{
	// PREVIOUS LOOP VARIABLES
	static bool rvs_p = false;
	static bool fwd_p = false;
	static bool stop_p = true;
	static int32_t duty_p = MOTOR_OFF;

	// CURRENT LOOP VARIABLES
	bool rvs = false;
	bool fwd = false;
	bool stop = true;
	bool direction_changed = false;
	int32_t duty = (int32_t)input;
	bool speed_changed = false;

	// CHECK FOR OVERRIDE CONDITIONS
	if (duty == 0 || status.faultInput == true || status.faultBatt == true)
	{
		duty = RADIO_CENTER;
	}

	// TRUNCATE RADIO INPUT TO LIMITS
	if (duty > RADIO_MAX)
	{
		duty = RADIO_MAX;
	}
	else if (duty < RADIO_MIN)
	{
		duty = RADIO_MIN;
	}

	// PROCESS INPUT TO MOTOR PWM
	if (duty >= (RADIO_CENTER - RADIO_HYST) && duty <= (RADIO_CENTER + RADIO_HYST))
	{
		duty = MOTOR_OFF;
		stop = true;
		fwd = false;
		rvs = false;
	}
	else if (duty < (RADIO_CENTER - RADIO_HYST))
	{
		duty = RADIO_CENTER - duty;
		stop = false;
		rvs = true;
		fwd = false;
	}
	else
	{
		duty = duty - RADIO_CENTER;
		stop = false;
		rvs = false;
		fwd = true;
	}


	// SET THE DIRECTION CHANGE FLAG
	if (rvs == rvs_p && fwd == fwd_p)
	{
		direction_changed = false;
	}
	else
	{
		direction_changed = true;
	}

	// SET THE SPEED CHANGE FLAG
	if (duty == duty_p)
	{
		speed_changed = false;
	}
	else
	{
		speed_changed = true;
	}

	// UPDATE THE MOTOR
	if (speed_changed || direction_changed)
	{
		if (duty == MOTOR_OFF)
		{
			MOTOR_TurnOFF();
		}
		else if (speed_changed && !direction_changed)
		{
			MOTOR_UpdatePWM(duty);
		}
		else //(direction_changed)
		{
			MOTOR_DirectionChanged(duty, fwd);
		}
	}

	// UPDATE STATUS VARIABLES
	duty_p = duty;
	fwd_p = fwd;
	rvs_p = rvs;
	stop_p = stop;
}

/*
 * PRIVATE FUNCTIONS
 */

void MOTOR_TurnOFF(void)
{
	TIM_Stop(TIM_MOTOR);
	TIM_OnPulse(TIM_MOTOR, TIM_MOTOR_CH, MOTOR_TimerBlankIRQ);
	TIM_OnReload(TIM_MOTOR, MOTOR_TimerBlankIRQ);
	TIM_SetPulse(TIM_MOTOR, TIM_MOTOR_CH, 0);
	TIM_Deinit(TIM_MOTOR);

	GPIO_Reset(FET_P1_GPIO, FET_P1_PIN);
	GPIO_Reset(FET_N2_GPIO, FET_N2_PIN);
	GPIO_Reset(FET_P2_GPIO, FET_P2_PIN);
	GPIO_Reset(FET_N1_GPIO, FET_N1_PIN);
	CORE_Delay(10);

	if (MOTOR_BRAKING)
	{
		GPIO_Set(FET_N1_GPIO, FET_N1_PIN);
		GPIO_Set(FET_N2_GPIO, FET_N2_PIN);
		CORE_Delay(5);
	}
}

void MOTOR_UpdatePWM(int32_t d)
{
	TIM_SetPulse(TIM_MOTOR, TIM_MOTOR_CH, d);
}

void MOTOR_DirectionChanged(int32_t d, bool fwd)
{
	if (fwd) // going forward
	{
		TIM_Stop(TIM_MOTOR);
		TIM_OnPulse(TIM_MOTOR, TIM_MOTOR_CH, MOTOR_TimerBlankIRQ);
		TIM_OnReload(TIM_MOTOR, MOTOR_TimerBlankIRQ);
		TIM_SetPulse(TIM_MOTOR, TIM_MOTOR_CH, 0);
		TIM_Deinit(TIM_MOTOR);

		GPIO_Reset(FET_P1_GPIO, FET_P1_PIN);
		GPIO_Reset(FET_P2_GPIO, FET_P2_PIN);
		GPIO_Reset(FET_N1_GPIO, FET_N1_PIN);
		GPIO_Reset(FET_N2_GPIO, FET_N2_PIN);
		CORE_Delay(10);
		GPIO_Set(FET_P1_GPIO, FET_P1_PIN);
		CORE_Delay(5);

		TIM_Init(TIM_MOTOR, TIM_MOTOR_FREQ, TIM_MOTOR_RELOAD);
		TIM_OnPulse(TIM_MOTOR, TIM_MOTOR_CH, MOTOR_N2TimerPulseISR);
		TIM_OnReload(TIM_MOTOR, MOTOR_N2TimerReloadISR);
		TIM_SetPulse(TIM_MOTOR, TIM_MOTOR_CH, d);
		TIM_Start(TIM_MOTOR);
	}
	else // going reverse
	{
		TIM_Stop(TIM_MOTOR);
		TIM_OnPulse(TIM_MOTOR, TIM_MOTOR_CH, MOTOR_TimerBlankIRQ);
		TIM_OnReload(TIM_MOTOR, MOTOR_TimerBlankIRQ);
		TIM_SetPulse(TIM_MOTOR, TIM_MOTOR_CH, 0);
		TIM_Deinit(TIM_MOTOR);

		GPIO_Reset(FET_P1_GPIO, FET_P1_PIN);
		GPIO_Reset(FET_P2_GPIO, FET_P2_PIN);
		GPIO_Reset(FET_N1_GPIO, FET_N1_PIN);
		GPIO_Reset(FET_N2_GPIO, FET_N2_PIN);
		CORE_Delay(10);
		GPIO_Set(FET_P2_GPIO, FET_P2_PIN);
		CORE_Delay(5);

		TIM_Init(TIM_MOTOR, TIM_MOTOR_FREQ, TIM_MOTOR_RELOAD);
		TIM_OnPulse(TIM_MOTOR, TIM_MOTOR_CH, MOTOR_N1TimerPulseISR);
		TIM_OnReload(TIM_MOTOR, MOTOR_N1TimerReloadISR);
		TIM_SetPulse(TIM_MOTOR, TIM_MOTOR_CH, d);
		TIM_Start(TIM_MOTOR);
	}
}

/*
 * INTERRUPT ROUTINES
 */

void MOTOR_N2TimerPulseISR (void)
{
	GPIO_Reset(FET_N2_GPIO, FET_N2_PIN);
}

void MOTOR_N2TimerReloadISR (void)
{
	GPIO_Set(FET_N2_GPIO, FET_N2_PIN);
}

void MOTOR_N1TimerPulseISR (void)
{
	GPIO_Reset(FET_N1_GPIO, FET_N1_PIN);
}

void MOTOR_N1TimerReloadISR (void)
{
	GPIO_Set(FET_N1_GPIO, FET_N1_PIN);
}

void MOTOR_TimerBlankIRQ (void)
{
	// Intentionally left blank
}

/* ~~~~~~~~~~~~~~~~~~~~~~~~~~~~~~~~~~~~~~~~~~~~~~~~~~ */

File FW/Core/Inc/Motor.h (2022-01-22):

/* ~~~~~~~~~~~~~~~~~~~~~~~~~~~~~~~~~~~~~~~~~~~~~~~~~~ */
#ifndef MOTOR_H
#define MOTOR_H
/* ~~~~~~~~~~~~~~~~~~~~~~~~~~~~~~~~~~~~~~~~~~~~~~~~~~ */

#include "STM32X.h"

/*
 * PUBLIC DEFINITIONS
 */

#define MOTOR_PERIOD_MS		10

#define MOTOR_OFF			0
#define MOTOR_MIN			MOTOR_OFF
#define MOTOR_MAX			TIM_MOTOR_RELOAD

#define MOTOR_OFF_ERROR			50
#define MOTOR_OFF_HYST			10
#define MOTOR_MAX_ERROR			10

/*
 * PUBLIC TYPES
 */

/*
 * PUBLIC FUNCTIONS
 */

void MOTOR_Init (void);
void MOTOR_Update (void);

/*
 * EXTERN DECLARATIONS
 */

/* ~~~~~~~~~~~~~~~~~~~~~~~~~~~~~~~~~~~~~~~~~~~~~~~~~~ */
#endif /* MOTOR_H */
/* ~~~~~~~~~~~~~~~~~~~~~~~~~~~~~~~~~~~~~~~~~~~~~~~~~~ */

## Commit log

2021-10-17 Initial WIP Commit
    [THE_BRAWN.kicad_pcb, THE_BRAWN.sch]
2021-10-23 Sync file structure
    [THE_BRAWN.kicad_pcb, THE_BRAWN.sch]
2022-01-01 WIP Update STM32 Project
2022-01-22 Upload HW Files
    [BRAINS - Bill of Materials - SINGLE-BRAWN(Default).xlsx, BRAINS - Bill of Materials-BRAWN(Default).xlsx, BRAWN(Default).step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]
2022-01-22 CAD Design for Programming Clip
    [Programmer Clip.SLDPRT, Programmer ClipBottom.3MF, Programmer ClipTop.3MF]
